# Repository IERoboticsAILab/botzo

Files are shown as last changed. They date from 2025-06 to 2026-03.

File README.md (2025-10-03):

<div align="center">
<h1>BOTZO 🐾</h1>

**`The good boy quadruped robot :)`**

<p align="center">
    <a href="https://www.instagram.com/botzo.ie/" target="_blank" rel="noopener noreferrer">
        
    </a>
    <a href="https://www.youtube.com/@Botzoie" target="_blank" rel="noopener noreferrer">
        
    </a>
    <a href="mailto:botzoteam@gmail.com">
        
    </a>
    <a href="">
        
    </a>

</p>

🚨🚧 **Project Under Construction!** 🚧🚨

Here's a sneak peek of our current progress:

</div>

> [!NOTE]
> A new documentation is currently being written 😃. It is already available [here](https://IERoboticsAILab.github.io/botzo/)

<p align="center">
    <a href="https://github.com/IERoboticsAILab/botzo/blob/main/docs/assets/botzo_new_final_design.png">
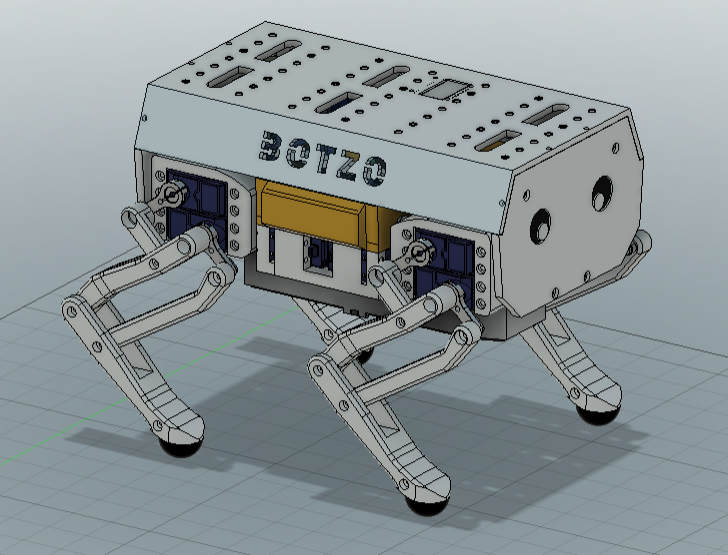
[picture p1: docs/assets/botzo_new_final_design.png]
Botzo
        
    </a>
</p>

> Stay tuned for updates and feel free to reach out with suggestions! Let's build Botzo together! 🛠️

## 🌟 **Welcome to the Botzo Project!**

**Botzo** is an autonomous quadruped robot designed to Navigate and Interact with its environment 🌍

This project combines sleek design, cutting-edge technology, and practical functionality to redefine robotic mobility.

## 📚 **Project Overview**

Botzo's development is divided into multiple phases, each focusing on specific aspects of its design, hardware, and software. We're actively working through these stages to bring the robot to life!

We stand in the middle of a trade of between high quality software and hardware, with low cost and affordability.

**Botzo is aimed to be a strong platform for everyone to replicate under 500€**

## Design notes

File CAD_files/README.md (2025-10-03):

<div align="center">
<h1>BOTZO 🐾</h1>

**`The good boy quadruped robot :)`**

<p align="center">
    <a href="https://www.instagram.com/botzo.ie/" target="_blank" rel="noopener noreferrer">
        
    </a>
    <a href="" target="_blank" rel="noopener noreferrer">
        
    </a>
    <a href="mailto:botzoteam@gmail.com">
        
    </a>
    <a href="">
        
    </a>

more about botzo [here](https://github.com/IERoboticsAILab/botzo)

for specific CAD documentation [here](https://ieroboticsailab.github.io/botzo/build/cad/cad-model/)

botzo

</p>
</div>

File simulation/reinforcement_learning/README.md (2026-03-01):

<div align="center">
<h1>BOTZO 🐾</h1>

**`The good boy quadruped robot :)`**

<p align="center">
    <a href="https://www.instagram.com/botzo.ie/" target="_blank" rel="noopener noreferrer">
        
    </a>
    <a href="" target="_blank" rel="noopener noreferrer">
        
    </a>
    <a href="mailto:botzoteam@gmail.com">
        
    </a>
    <a href="">
        
    </a>

</p>

</div>

more [here](https://github.com/IERoboticsAILab/botzo)

# Reinforcement Learning
In this repo we will explore how we teach botzo to walk

## Resources

- Genesis [link](https://genesis-world.readthedocs.io/en/latest/user_guide/index.html)
- Basics [link](https://youtu.be/f6LkEQsXGF8?si=eqC7IzNiBTZROUgm)
- theconstrucsim course Intermediate Generative AI for Robotics [link](https://app.theconstruct.ai/courses/intermediate-generative-ai-for-robotics-276/)
- theconstrucsim course Mastering Reinforcement Learning for Robotics [link](https://app.theconstruct.ai/courses/mastering-reinforcement-learning-for-robotics-286/)
- [Isaac Sim](https://docs.isaacsim.omniverse.nvidia.com/4.5.0/index.html)

# Isaac Sim

<p align="center">
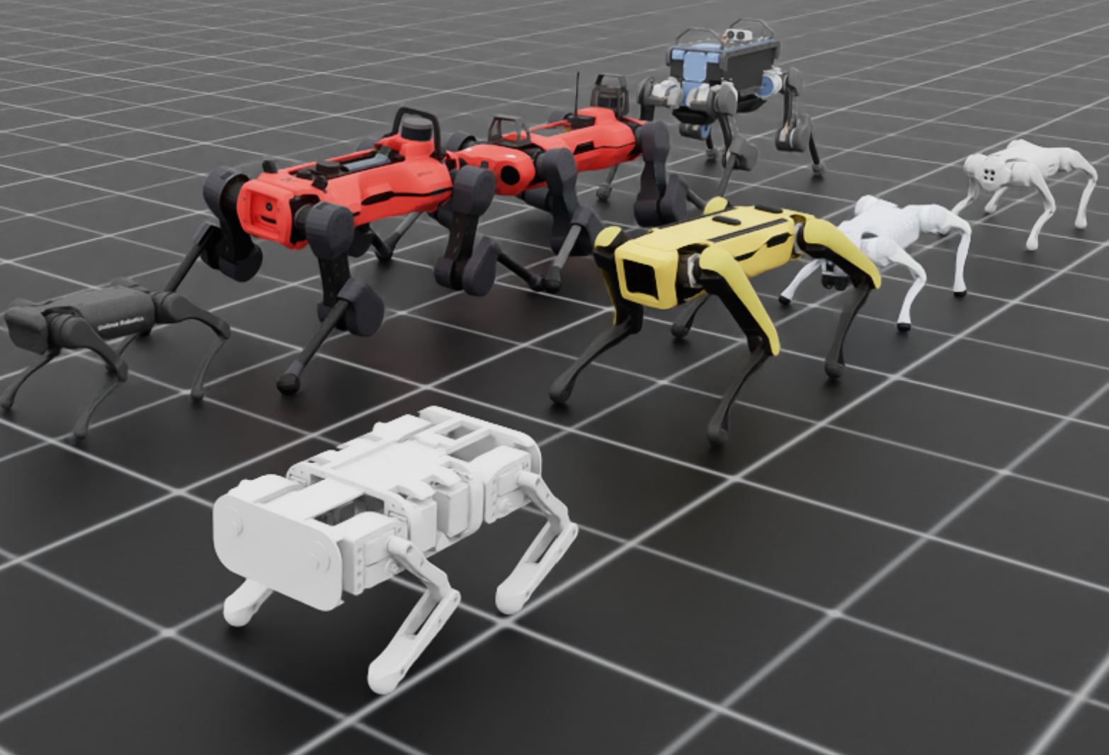
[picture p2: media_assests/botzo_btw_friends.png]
  
</p>
<p align="center"><em>Botzo between the giants & friends</em></p>

Computer specifications:
| Component | Specification |
|---|---|
| RAM | 64GB |
| GPU | RTX 4090 |
| VRAM | 16GB |
| OS | Windows 11 |
| Storage | 1TB |

>_Check system requirements compatibility and satisfaction with [this](https://download.isaacsim.omniverse.nvidia.com/isaac-sim-comp-check%404.5.0-rc.6%2Brelease.675.f1cca148.gl.windows-x86_64.release.zip)_

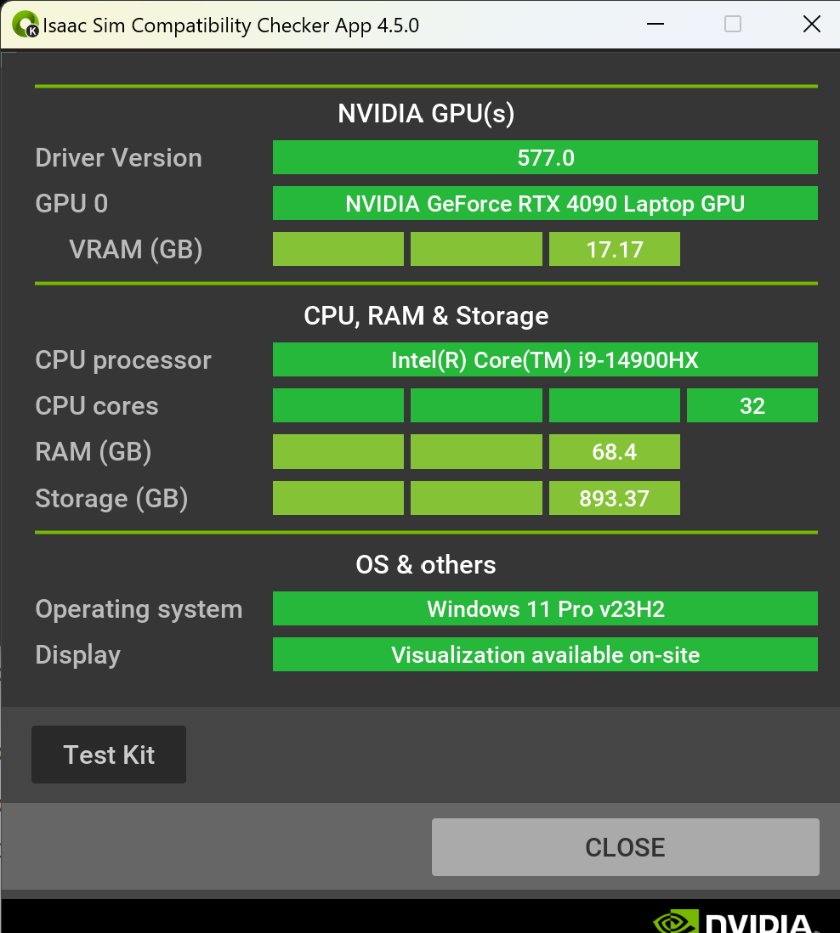
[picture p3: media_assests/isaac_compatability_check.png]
ours


Download [IsaacSim](https://download.isaacsim.omniverse.nvidia.com/isaac-sim-standalone%404.5.0-rc.36%2Brelease.19112.f59b3005.gl.windows-x86_64.release.zip) for your OS

```shell
mkdir C:\isaacsim
cd %USERPROFILE%/Downloads
tar -xvzf "isaac-sim-standalone@4.5.0-rc.36+release.19112.f59b3005.gl.windows-x86_64.release.zip" -C C:\isaacsim
cd C:\isaacsim
post_install.bat
isaac-sim.selector.bat
```
> [!NOTE] 
>The Isaac Sim app can be run directly via command line with `isaac-sim.bat`. Start new empty simulation.

> [!NOTE] 
>_extension_examples_ and _standalone_examples_ folder for the tutorials (ex: `.\python.bat .\standalone_examples\api\isaacsim.asset.importer.urdf\urdf_import.py`)

### Getting started with Isaac Sim

For more tutorials: Documentation [here](https://docs.isaacsim.omniverse.nvidia.com/4.5.0/introduction/quickstart_index.html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)

`conda activate env_isaaclab`

#### Import URDF

`.\python.bat ..\Users\grego\Desktop\GRINGO\botzo\botzo\simulation\reinforcment_learning\standalone_examples\import_botzo_urdf.py`

And then save it as a USD file. This file is used to import and manipulate your robot in Isaac Lab using python APIs. 

#### Import USD

`.\python.bat ..\Users\grego\Desktop\GRINGO\botzo\botzo\simulation\reinforcment_learning\standalone_examples\load_botzo_usd.py --usd_path "C:\Users\grego\Desktop\GRINGO\botzo\botzo\simulation\reinforcment_learning\botzo_USD\botzo_USD.usd"`

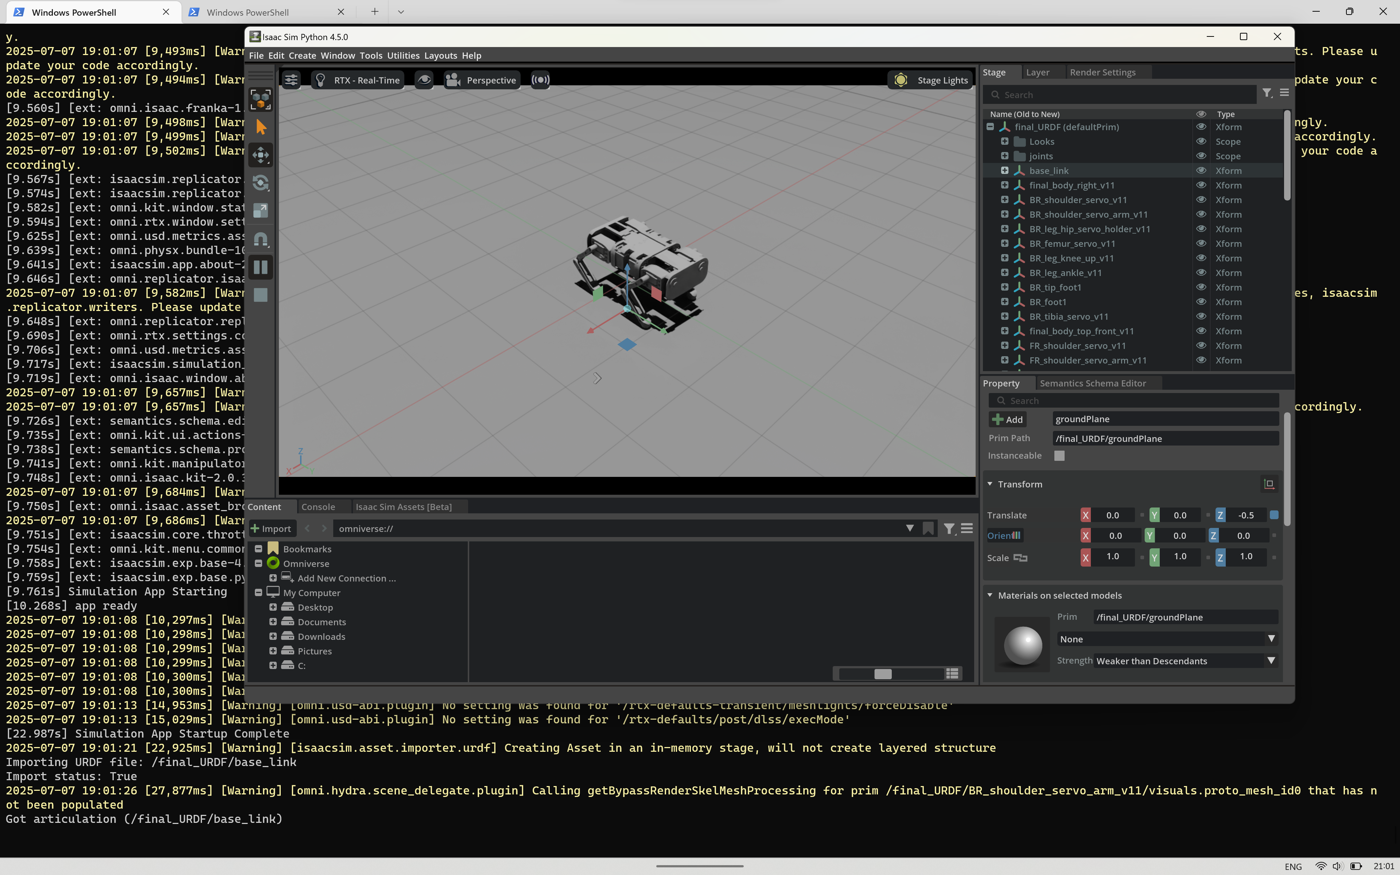
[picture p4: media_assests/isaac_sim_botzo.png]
result


<br>

<br>

# Isaac Lab

Isaac Lab is a collection of tools and libraries for building and simulating robots in Isaac Sim. It provides a set of APIs for creating robots, sensors, and environments, as well as tools for training and deploying reinforcement learning agents.

After the installation of Isaac Sim and Isaac Lab, you run examples such as:

```shell
(env_isaaclab) C:\Users\grego\Desktop\GRINGO\IsaacLab\IsaacLab>python scripts\tutorials\03_envs\create_quadruped_base_env.py
```

example

## Create your robot Configuration

To import your custom robot it is recomended to create a new Robot configuration python script.

Go to isaaclab/source/isaaclab_assets/robots and create a new python file with the name of your robot, for example `botzo.py`. Here we will import the USD file, and set robot properties.

<details>
<summary><b> `botzo.py` Code Robot configuration script </b></summary>

[Full Code](https://github.com/GRINGOLOCO7/IsaacLab/blob/main/source/isaaclab_assets/isaaclab_assets/robots/botzo.py)

```python

import isaaclab.sim as sim_utils
from isaaclab.actuators import ImplicitActuatorCfg
from isaaclab.assets.articulation import ArticulationCfg

stiffness = 2000.0     # N⋅m/rad - Very stiff for standing
damping = 200.0        # N⋅m⋅s/rad - High damping for stability
effort_limit_sim = 4.0 # N⋅m - Allow higher than rated for simulation
velocity_limit_sim = 10.0 # rad/s - Slightly higher for responsiveness

stiffness *= 40
damping *= 15
effort_limit_sim *= 25
velocity_limit_sim *= 10

BOTZO_CONFIG = ArticulationCfg(
    spawn=sim_utils.UsdFileCfg(
        usd_path="C:\\Users\\grego\\Desktop\\GRINGO\\botzo\\botzo\\simulation\\reinforcement_learning\\botzo_USD\\botzo_USD.usd",
        scale=(0.3, 0.3, 0.3),
    ),
    init_state=ArticulationCfg.InitialStateCfg(
        joint_pos={
            "BL_shoulder_joint": 0.0,
            "BL_femur_joint": 0.0,
            "BL_knee_joint": 0.0,

            "BR_shoulder_joint": 0.0,
            "BR_femur_joint": 0.0,
            "Revolute_43": 0.0,

            "FL_shoulder_joint": 0.0,
            "FL_femur_joint": 0.0,
            "FL_knee_joint": 0.0,

            "FR_shoulder_joint": 0.0,
            "FR_femur_joint": 0.0,
            "FR_knee_joint": 0.0,
        },
        pos=(0.0, 0.0, 0.25),
        # rotate 90 degrees around the x-axis
        rot=(-0.7071, 0.0, 0.0, 0.7071),  # Quaternion for 90 degrees rotation around x-axis
        # rotate upside down
        #rot=(0.0, 1.0, 0.0, 0.0),
    ),
    actuators={
        "BL_shoulder_act": ImplicitActuatorCfg(joint_names_expr=["BL_shoulder_joint"],effort_limit_sim=effort_limit_sim, velocity_limit_sim=velocity_limit_sim, stiffness=stiffness, damping=damping),
        "BL_femur_act": ImplicitActuatorCfg(joint_names_expr=["BL_femur_joint"], effort_limit_sim=effort_limit_sim, velocity_limit_sim=velocity_limit_sim, stiffness=stiffness, damping=damping),
        "BL_knee_act": ImplicitActuatorCfg(joint_names_expr=["BL_knee_joint"], effort_limit_sim=effort_limit_sim, velocity_limit_sim=velocity_limit_sim, stiffness=stiffness, damping=damping),
        "BR_shoulder_act": ImplicitActuatorCfg(joint_names_expr=["BR_shoulder_joint"], effort_limit_sim=effort_limit_sim, velocity_limit_sim=velocity_limit_sim, stiffness=stiffness, damping=damping),
        "BR_femur_act": ImplicitActuatorCfg(joint_names_expr=["BR_femur_joint"], effort_limit_sim=effort_limit_sim, velocity_limit_sim=velocity_limit_sim, stiffness=stiffness, damping=damping),
        "Revolute_43_act": ImplicitActuatorCfg(joint_names_expr=["Revolute_43"], effort_limit_sim=effort_limit_sim, velocity_limit_sim=velocity_limit_sim, stiffness=stiffness, damping=damping),
        "FL_shoulder_act": ImplicitActuatorCfg(joint_names_expr=["FL_shoulder_joint"], effort_limit_sim=effort_limit_sim, velocity_limit_sim=velocity_limit_sim, stiffness=stiffness, damping=damping),
        "FL_femur_act": ImplicitActuatorCfg(joint_names_expr=["FL_femur_joint"], effort_limit_sim=effort_limit_sim, velocity_limit_sim=velocity_limit_sim, stiffness=stiffness, damping=damping),
        "FL_knee_act": ImplicitActuatorCfg(joint_names_expr=["FL_knee_joint"], effort_limit_sim=effort_limit_sim, velocity_limit_sim=velocity_limit_sim, stiffness=stiffness, damping=damping),
        "FR_shoulder_act": ImplicitActuatorCfg(joint_names_expr=["FR_shoulder_joint"], effort_limit_sim=effort_limit_sim, velocity_limit_sim=velocity_limit_sim, stiffness=stiffness, damping=damping),
        "FR_femur_act": ImplicitActuatorCfg(joint_names_expr=["FR_femur_joint"], effort_limit_sim=effort_limit_sim, velocity_limit_sim=velocity_limit_sim, stiffness=stiffness, damping=damping),
        "FR_knee_act": ImplicitActuatorCfg(joint_names_expr=["FR_knee_joint"], effort_limit_sim=effort_limit_sim, velocity_limit_sim=velocity_limit_sim, stiffness=stiffness, damping=damping),
    },
)

```

</details>

<br>

<details>
<summary><b> `dofrobot.py` Code Robot configuration script </b></summary>

[Full Code](https://github.com/GRINGOLOCO7/IsaacLab/blob/main/source/isaaclab_assets/isaaclab_assets/robots/dofrobot.py)

```python

import isaaclab.sim as sim_utils
from isaaclab.actuators import ImplicitActuatorCfg
from isaaclab.assets.articulation import ArticulationCfg
from isaaclab.utils.assets import ISAAC_NUCLEUS_DIR

DOFBOT_CONFIG = ArticulationCfg(
    spawn=sim_utils.UsdFileCfg(
        usd_path=f"{ISAAC_NUCLEUS_DIR}/Robots/Dofbot/dofbot.usd",
        rigid_props=sim_utils.RigidBodyPropertiesCfg(
            disable_gravity=False,
            max_depenetration_velocity=5.0,
        ),
        articulation_props=sim_utils.ArticulationRootPropertiesCfg(
            enabled_self_collisions=True, solver_position_iteration_count=8, solver_velocity_iteration_count=0
        ),
    ),
    init_state=ArticulationCfg.InitialStateCfg(
        joint_pos={
            "joint1": 0.0,
            "joint2": 0.0,
            "joint3": 0.0,
            "joint4": 0.0,
        },
        pos=(0.25, -0.25, 0.0),
    ),
    actuators={
        "front_joints": ImplicitActuatorCfg(
            joint_names_expr=["joint[1-2]"],
            effort_limit_sim=100.0,
            velocity_limit_sim=100.0,
            stiffness=10000.0,
            damping=100.0,
        ),
        "joint3_act": ImplicitActuatorCfg(
            joint_names_expr=["joint3"],
            effort_limit_sim=100.0,
            velocity_limit_sim=100.0,
            stiffness=10000.0,
            damping=100.0,
        ),
        "joint4_act": ImplicitActuatorCfg(
            joint_names_expr=["joint4"],
            effort_limit_sim=100.0,
            velocity_limit_sim=100.0,
            stiffness=10000.0,
            damping=100.0,
        ),
    },
)

```

</details>

<br>

<details>
<summary><b> `jetbot.py` Code Robot configuration script </b></summary>

[Full Code](https://github.com/GRINGOLOCO7/IsaacLab/blob/main/source/isaaclab_assets/isaaclab_assets/robots/jetbot.py)

```python

import isaaclab.sim as sim_utils
from isaaclab.assets import ArticulationCfg
from isaaclab.actuators import ImplicitActuatorCfg
from isaaclab.utils.assets import ISAAC_NUCLEUS_DIR

JETBOT_CONFIG = ArticulationCfg(
    spawn=sim_utils.UsdFileCfg(usd_path=f"{ISAAC_NUCLEUS_DIR}/Robots/Jetbot/jetbot.usd"),
    actuators={"wheel_acts": ImplicitActuatorCfg(joint_names_expr=[".*"], damping=None, stiffness=None)},
)

```

</details>

### Use your robot configuration

Now that we configured our robot, we can simply import it and use it in any python file we want

1. Import robot config: `from isaaclab_assets.robots.botzo import BOTZO_CONFIG`
2. Spawn robot: `Botzo = BOTZO_CONFIG.replace(prim_path="{ENV_REGEX_NS}/Botzo")`
3. Now you can move and interact with it

#### Our Examples:

1. `python scripts\demos\quadrupeds.py`

<details>
<summary><b> Spawn various robots </b></summary>

[Full Code](https://github.com/GRINGOLOCO7/IsaacLab/blob/main/scripts/demos/quadrupeds.py)

```python
# Copyright (c) 2022-2025, The Isaac Lab Project Developers (https://github.com/isaac-sim/IsaacLab/blob/main/CONTRIBUTORS.md).
# All rights reserved.
#
# SPDX-License-Identifier: BSD-3-Clause

"""
This script demonstrates different legged robots.

.. code-block:: bash

    # Usage
    ./isaaclab.sh -p scripts/demos/quadrupeds.py

"""

"""Launch Isaac Sim Simulator first."""

import argparse

from isaaclab.app import AppLauncher

# add argparse arguments
parser = argparse.ArgumentParser(description="This script demonstrates different legged robots.")
# append AppLauncher cli args
AppLauncher.add_app_launcher_args(parser)
# parse the arguments
args_cli = parser.parse_args()

# launch omniverse app
app_launcher = AppLauncher(args_cli)
simulation_app = app_launcher.app

"""Rest everything follows."""

import numpy as np
import torch

import isaacsim.core.utils.prims as prim_utils

import isaaclab.sim as sim_utils
from isaaclab.assets import Articulation

##
# Pre-defined configs
##
from isaaclab_assets.robots.anymal import ANYMAL_B_CFG, ANYMAL_C_CFG, ANYMAL_D_CFG  # isort:skip
from isaaclab_assets.robots.spot import SPOT_CFG  # isort:skip
from isaaclab_assets.robots.unitree import UNITREE_A1_CFG, UNITREE_GO1_CFG, UNITREE_GO2_CFG  # isort:skip
from isaaclab_assets.robots.botzo import BOTZO_CONFIG  # isort:skip

def define_origins(num_origins: int, spacing: float) -> list[list[float]]:
    """Defines the origins of the scene."""
    # create tensor based on number of environments
    env_origins = torch.zeros(num_origins, 3)
    # create a grid of origins
    num_cols = np.floor(np.sqrt(num_origins))
    num_rows = np.ceil(num_origins / num_cols)
    xx, yy = torch.meshgrid(torch.arange(num_rows), torch.arange(num_cols), indexing="xy")
    env_origins[:, 0] = spacing * xx.flatten()[:num_origins] - spacing * (num_rows - 1) / 2
    env_origins[:, 1] = spacing * yy.flatten()[:num_origins] - spacing * (num_cols - 1) / 2
    env_origins[:, 2] = 0.0
    # return the origins
    return env_origins.tolist()

def design_scene() -> tuple[dict, list[list[float]]]:
    """Designs the scene."""
    # Ground-plane
    cfg = sim_utils.GroundPlaneCfg()
    cfg.func("/World/defaultGroundPlane", cfg)
    # Lights
    cfg = sim_utils.DomeLightCfg(intensity=2000.0, color=(0.75, 0.75, 0.75))
    cfg.func("/World/Light", cfg)

    # Create separate groups called "Origin1", "Origin2", "Origin3"
    # Each group will have a mount and a robot on top of it
    origins = define_origins(num_origins=8, spacing=1.25)

    # Origin 1 with Anymal B
    prim_utils.create_prim("/World/Origin1", "Xform", translation=origins[0])
    # -- Robot
    anymal_b = Articulation(ANYMAL_B_CFG.replace(prim_path="/World/Origin1/Robot"))

    # Origin 2 with Anymal C
    prim_utils.create_prim("/World/Origin2", "Xform", translation=origins[1])
    # -- Robot
    anymal_c = Articulation(ANYMAL_C_CFG.replace(prim_path="/World/Origin2/Robot"))

    # Origin 3 with Anymal D
    prim_utils.create_prim("/World/Origin3", "Xform", translation=origins[2])
    # -- Robot
    anymal_d = Articulation(ANYMAL_D_CFG.replace(prim_path="/World/Origin3/Robot"))

    # Origin 4 with Unitree A1
    prim_utils.create_prim("/World/Origin4", "Xform", translation=origins[3])
    # -- Robot
    unitree_a1 = Articulation(UNITREE_A1_CFG.replace(prim_path="/World/Origin4/Robot"))

    # Origin 5 with Unitree Go1
    prim_utils.create_prim("/World/Origin5", "Xform", translation=origins[4])
    # -- Robot
    unitree_go1 = Articulation(UNITREE_GO1_CFG.replace(prim_path="/World/Origin5/Robot"))

    # Origin 6 with Unitree Go2
    prim_utils.create_prim("/World/Origin6", "Xform", translation=origins[5])
    # -- Robot
    unitree_go2 = Articulation(UNITREE_GO2_CFG.replace(prim_path="/World/Origin6/Robot"))

    # Origin 7 with Boston Dynamics Spot
    prim_utils.create_prim("/World/Origin7", "Xform", translation=origins[6])
    # -- Robot
    spot = Articulation(SPOT_CFG.replace(prim_path="/World/Origin7/Robot"))

    # Origin 8 with Botzo
    prim_utils.create_prim("/World/Origin8", "Xform", translation=origins[7])
    # -- Robot
    botzo = Articulation(BOTZO_CONFIG.replace(prim_path="/World/Origin8/Robot"))

    # return the scene information
    scene_entities = {
        "anymal_b": anymal_b,
        "anymal_c": anymal_c,
        "anymal_d": anymal_d,
        "unitree_a1": unitree_a1,
        "unitree_go1": unitree_go1,
        "unitree_go2": unitree_go2,
        "spot": spot,
        "botzo": botzo,
    }
    return scene_entities, origins

def run_simulator(sim: sim_utils.SimulationContext, entities: dict[str, Articulation], origins: torch.Tensor):
    """Runs the simulation loop."""
    # Define simulation stepping
    sim_dt = sim.get_physics_dt()
    sim_time = 0.0
    count = 0
    # Simulate physics
    while simulation_app.is_running():
        # reset
        if count % 200 == 0:
            # reset counters
            sim_time = 0.0
            count = 0
            # reset robots
            for index, robot in enumerate(entities.values()):
                # root state
                root_state = robot.data.default_root_state.clone()
                root_state[:, :3] += origins[index]
                robot.write_root_pose_to_sim(root_state[:, :7])
                robot.write_root_velocity_to_sim(root_state[:, 7:])
                # joint state
                joint_pos, joint_vel = robot.data.default_joint_pos.clone(), robot.data.default_joint_vel.clone()
                robot.write_joint_state_to_sim(joint_pos, joint_vel)
                # reset the internal state
                robot.reset()
            print("[INFO]: Resetting robots state...")
        # apply default actions to the quadrupedal robots
        for robot in entities.values():
            # generate random joint positions
            joint_pos_target = robot.data.default_joint_pos + torch.randn_like(robot.data.joint_pos) * 0.1
            # apply action to the robot
            robot.set_joint_position_target(joint_pos_target)
            # write data to sim
            robot.write_data_to_sim()
        # perform step
        sim.step()
        # update sim-time
        sim_time += sim_dt
        count += 1
        # update buffers
        for robot in entities.values():
            robot.update(sim_dt)

def main():
    """Main function."""

    # Initialize the simulation context
    sim = sim_utils.SimulationContext(sim_utils.SimulationCfg(dt=0.01))
    # Set main camera
    sim.set_camera_view(eye=[2.5, 2.5, 2.5], target=[0.0, 0.0, 0.0])
    # design scene
    scene_entities, scene_origins = design_scene()
    scene_origins = torch.tensor(scene_origins, device=sim.device)
    # Play the simulator
    sim.reset()
    # Now we are ready!
    print("[INFO]: Setup complete...")
    # Run the simulator
    run_simulator(sim, scene_entities, scene_origins)

if __name__ == "__main__":
    # run the main function
    main()
    # close sim app
    simulation_app.close()

```

</details>

2. `python scripts\tutorials\01_assets\add_new_robot.py`

<details>
<summary><b> Spawn various robots and move them </b></summary>

[full Code](https://github.com/GRINGOLOCO7/IsaacLab/blob/main/scripts/tutorials/01_assets/add_new_robot.py)

```python
# Copyright (c) 2022-2025, The Isaac Lab Project Developers (https://github.com/isaac-sim/IsaacLab/blob/main/CONTRIBUTORS.md).
# All rights reserved.
#
# SPDX-License-Identifier: BSD-3-Clause

import argparse

from isaaclab.app import AppLauncher

# add argparse arguments
parser = argparse.ArgumentParser(
    description="This script demonstrates adding a custom robot to an Isaac Lab environment."
)
parser.add_argument("--num_envs", type=int, default=1, help="Number of environments to spawn.")
# append AppLauncher cli args
AppLauncher.add_app_launcher_args(parser)
# parse the arguments
args_cli = parser.parse_args()

# launch omniverse app
app_launcher = AppLauncher(args_cli)
simulation_app = app_launcher.app

import numpy as np
import torch

import isaaclab.sim as sim_utils
from isaaclab.actuators import ImplicitActuatorCfg
from isaaclab.assets import AssetBaseCfg
from isaaclab.assets.articulation import ArticulationCfg
from isaaclab.scene import InteractiveScene, InteractiveSceneCfg
from isaaclab.utils.assets import ISAAC_NUCLEUS_DIR

from isaaclab_assets.robots.botzo import BOTZO_CONFIG # source\isaaclab_assets\isaaclab_assets\robots\botzo.py

JETBOT_CONFIG = ArticulationCfg(
    spawn=sim_utils.UsdFileCfg(usd_path=f"{ISAAC_NUCLEUS_DIR}/Robots/Jetbot/jetbot.usd"),
    actuators={"wheel_acts": ImplicitActuatorCfg(joint_names_expr=[".*"], damping=None, stiffness=None)},
)

DOFBOT_CONFIG = ArticulationCfg(
    spawn=sim_utils.UsdFileCfg(
        usd_path=f"{ISAAC_NUCLEUS_DIR}/Robots/Dofbot/dofbot.usd",
        rigid_props=sim_utils.RigidBodyPropertiesCfg(
            disable_gravity=False,
            max_depenetration_velocity=5.0,
        ),
        articulation_props=sim_utils.ArticulationRootPropertiesCfg(
            enabled_self_collisions=True, solver_position_iteration_count=8, solver_velocity_iteration_count=0
        ),
    ),
    init_state=ArticulationCfg.InitialStateCfg(
        joint_pos={
            "joint1": 0.0,
            "joint2": 0.0,
            "joint3": 0.0,
            "joint4": 0.0,
        },
        pos=(0.25, -0.25, 0.0),
    ),
    actuators={
        "front_joints": ImplicitActuatorCfg(
            joint_names_expr=["joint[1-2]"],
            effort_limit_sim=100.0,
            velocity_limit_sim=100.0,
            stiffness=10000.0,
            damping=100.0,
        ),
        "joint3_act": ImplicitActuatorCfg(
            joint_names_expr=["joint3"],
            effort_limit_sim=100.0,
            velocity_limit_sim=100.0,
            stiffness=10000.0,
            damping=100.0,
        ),
        "joint4_act": ImplicitActuatorCfg(
            joint_names_expr=["joint4"],
            effort_limit_sim=100.0,
            velocity_limit_sim=100.0,
            stiffness=10000.0,
            damping=100.0,
        ),
    },
)

class NewRobotsSceneCfg(InteractiveSceneCfg):
    """Designs the scene."""

    # Ground-plane
    ground = AssetBaseCfg(prim_path="/World/defaultGroundPlane", spawn=sim_utils.GroundPlaneCfg())

    # lights
    dome_light = AssetBaseCfg(
        prim_path="/World/Light", spawn=sim_utils.DomeLightCfg(intensity=3000.0, color=(0.75, 0.75, 0.75))
    )

    # robot
    Jetbot = JETBOT_CONFIG.replace(prim_path="{ENV_REGEX_NS}/Jetbot")
    Dofbot = DOFBOT_CONFIG.replace(prim_path="{ENV_REGEX_NS}/Dofbot")
    Botzo = BOTZO_CONFIG.replace(prim_path="{ENV_REGEX_NS}/Botzo")

def run_simulator(sim: sim_utils.SimulationContext, scene: InteractiveScene):
    sim_dt = sim.get_physics_dt()
    sim_time = 0.0
    count = 0

    while simulation_app.is_running():
        # reset
        if count % 500 == 0:
            # reset counters
            count = 0
            # reset the scene entities to their initial positions offset by the environment origins
            root_jetbot_state = scene["Jetbot"].data.default_root_state.clone()
            root_jetbot_state[:, :3] += scene.env_origins
            root_dofbot_state = scene["Dofbot"].data.default_root_state.clone()
            root_dofbot_state[:, :3] += scene.env_origins
            robot_botzo_state = scene["Botzo"].data.default_root_state.clone()
            robot_botzo_state[:, :3] += scene.env_origins

            # copy the default root state to the sim for the jetbot's orientation and velocity
            scene["Jetbot"].write_root_pose_to_sim(root_jetbot_state[:, :7])
            scene["Jetbot"].write_root_velocity_to_sim(root_jetbot_state[:, 7:])
            scene["Dofbot"].write_root_pose_to_sim(root_dofbot_state[:, :7])
            scene["Dofbot"].write_root_velocity_to_sim(root_dofbot_state[:, 7:])
            scene["Botzo"].write_root_pose_to_sim(robot_botzo_state[:, :7])
            scene["Botzo"].write_root_velocity_to_sim(robot_botzo_state[:, 7:])

            # copy the default joint states to the sim
            joint_pos, joint_vel = (
                scene["Jetbot"].data.default_joint_pos.clone(),
                scene["Jetbot"].data.default_joint_vel.clone(),
            )
            scene["Jetbot"].write_joint_state_to_sim(joint_pos, joint_vel)
            joint_pos, joint_vel = (
                scene["Dofbot"].data.default_joint_pos.clone(),
                scene["Dofbot"].data.default_joint_vel.clone(),
            )
            scene["Dofbot"].write_joint_state_to_sim(joint_pos, joint_vel)
            joint_pos, joint_vel = (
                scene["Botzo"].data.default_joint_pos.clone(),
                scene["Botzo"].data.default_joint_vel.clone(),
            )
            scene["Botzo"].write_joint_state_to_sim(joint_pos, joint_vel)
            # clear internal buffers
            scene.reset()
            print("[INFO]: Resetting Jetbot and Dofbot state...")

        # drive around
        if count % 100 < 75:
            # Drive straight by setting equal wheel velocities
            action = torch.Tensor([[10.0, 10.0]])
        else:
            # Turn by applying different velocities
            action = torch.Tensor([[5.0, -5.0]])

        scene["Jetbot"].set_joint_velocity_target(action)

        # wave
        wave_action = scene["Dofbot"].data.default_joint_pos
        wave_action[:, 0:4] = 0.25 * np.sin(2 * np.pi * 0.5 * sim_time)
        scene["Dofbot"].set_joint_position_target(wave_action)
        # move botzo
        botzo_action = scene["Botzo"].data.default_joint_pos
        botzo_action[:, 0:3] = 0.25 * np.sin(2 * np.pi * 0.5 * sim_time)
        botzo_action[:, 3:6] = 0.25 * np.cos(2 * np.pi * 0.5 * sim_time)
        scene["Botzo"].set_joint_position_target(botzo_action)

        scene.write_data_to_sim()
        sim.step()
        sim_time += sim_dt
        count += 1
        scene.update(sim_dt)

def main():
    """Main function."""
    # Initialize the simulation context
    sim_cfg = sim_utils.SimulationCfg(device=args_cli.device)
    sim = sim_utils.SimulationContext(sim_cfg)

    sim.set_camera_view([3.5, 0.0, 3.2], [0.0, 0.0, 0.5])
    # design scene
    scene_cfg = NewRobotsSceneCfg(args_cli.num_envs, env_spacing=2.0)
    scene = InteractiveScene(scene_cfg)
    # Play the simulator
    sim.reset()
    # Now we are ready!
    print("[INFO]: Setup complete...")
    # Run the simulator
    run_simulator(sim, scene)

if __name__ == "__main__":
    main()
    simulation_app.close()

```

</details>

3. `python scripts\tutorials\01_assets\botzo_move_IK.py `

<details>
<summary><b> Create digital twin of botzo and move it with our IK </b></summary>

https://github.com/GRINGOLOCO7/IsaacLab/blob/main/scripts/tutorials/01_assets/botzo_move_IK.py

```python
import argparse

from isaaclab.app import AppLauncher

# add argparse arguments
parser = argparse.ArgumentParser(
    description="This script demonstrates adding a custom robot to an Isaac Lab environment."
)
parser.add_argument("--num_envs", type=int, default=1, help="Number of environments to spawn.")
# append AppLauncher cli args
AppLauncher.add_app_launcher_args(parser)
# parse the arguments
args_cli = parser.parse_args()

# launch omniverse app
app_launcher = AppLauncher(args_cli)
simulation_app = app_launcher.app

import numpy as np
import torch

import isaaclab.sim as sim_utils
from isaaclab.actuators import ImplicitActuatorCfg
from isaaclab.assets import AssetBaseCfg
from isaaclab.assets.articulation import ArticulationCfg
from isaaclab.scene import InteractiveScene, InteractiveSceneCfg
from isaaclab.utils.assets import ISAAC_NUCLEUS_DIR

from isaaclab_assets.robots.botzo import BOTZO_CONFIG # source\isaaclab_assets\isaaclab_assets\robots\botzo.py
from botzo_IK_solver import *
import math

class NewRobotsSceneCfg(InteractiveSceneCfg):
    """Designs the scene."""

    # Ground-plane
    ground = AssetBaseCfg(prim_path="/World/defaultGroundPlane", spawn=sim_utils.GroundPlaneCfg())

    # lights
    dome_light = AssetBaseCfg(
        prim_path="/World/Light", spawn=sim_utils.DomeLightCfg(intensity=3000.0, color=(0.75, 0.75, 0.75))
    )

    # robot
    Botzo = BOTZO_CONFIG.replace(prim_path="{ENV_REGEX_NS}/Botzo")

def run_simulator(sim: sim_utils.SimulationContext, scene: InteractiveScene):
    sim_dt = sim.get_physics_dt()
    sim_time = 0.0
    count = 0

    idx = 0

    while simulation_app.is_running():
        # reset
        if count % 500 == 0:
            # reset counters
            count = 0
            # reset the scene entities to their initial positions offset by the environment origins
            robot_botzo_state = scene["Botzo"].data.default_root_state.clone()
            robot_botzo_state[:, :3] += scene.env_origins

            # copy the default root state to the sim for the jetbot's orientation and velocity
            scene["Botzo"].write_root_pose_to_sim(robot_botzo_state[:, :7])
            scene["Botzo"].write_root_velocity_to_sim(robot_botzo_state[:, 7:])

            # copy the default joint states to the sim
            joint_pos, joint_vel = (
                scene["Botzo"].data.default_joint_pos.clone(),
                scene["Botzo"].data.default_joint_vel.clone(),
            )
            scene["Botzo"].write_joint_state_to_sim(joint_pos, joint_vel)
            # clear internal buffers
            scene.reset()
            print("[INFO]: Resetting Botzo state...")

        # move botzo
        '''
        tensor([[
                0  -  BL_shoulder, 
                1  -  BR_shoulder, 
                2  -  FL_shoulder, 
                3  -  FR_shoulder, 

                4  -  BL_femur, 
                5  -  BR_femur, 
                6  -  FL_femur, 
                7  -  FR_femur, 

                8  -  BL_knee, 
                9  -  BR_knee, 
                10 -  FL_knee, 
                11 -  FR_knee
                ]], device='cuda:0')
        '''
        botzo_action = scene["Botzo"].data.default_joint_pos
        # print the difference btw current pos and target pos
        #print(f"{'='*10}\nCurrent: {scene['Botzo'].data.joint_pos},\nTarget: {botzo_action}\n{'='*10}\n\n\n")
        tolerance = math.radians(5.0)
        if not torch.all(torch.abs(scene["Botzo"].data.joint_pos - botzo_action) < tolerance):
            #print("position not reached")
            pass
        else:
            #print("position reached, pass to new target")
            # calculate angles
            FR_s_f_t = legIK(forward_targets_FR_BL[idx][0], forward_targets_FR_BL[idx][1], forward_targets_FR_BL[idx][2])
            FR_angle_shoulder, FR_angle_femur, FR_angle_knee = FR_s_f_t
            target_FR_angle_shoulder = math.radians(real_sim_angle(FR_angle_shoulder,joint_ids["FR"]["shoulder"]))
            target_FR_angle_femur = math.radians(real_sim_angle(FR_angle_femur, joint_ids["FR"]["femur"]))
            target_FR_angle_knee = math.radians(real_sim_angle(FR_angle_knee, joint_ids["FR"]["knee"]))
            FL_s_f_t = legIK(forward_targets_FL_BR[idx][0], forward_targets_FL_BR[idx][1], forward_targets_FL_BR[idx][2])
            FL_angle_shoulder, FL_angle_femur, FL_angle_knee = FL_s_f_t
            target_FL_angle_shoulder = math.radians(real_sim_angle(FL_angle_shoulder,joint_ids["FL"]["shoulder"]))
            target_FL_angle_femur = math.radians(real_sim_angle(FL_angle_femur, joint_ids["FL"]["femur"]))
            target_FL_angle_knee = math.radians(real_sim_angle(FL_angle_knee, joint_ids["FL"]["knee"]))
            BR_s_f_t = legIK(forward_targets_FL_BR[idx][0], forward_targets_FL_BR[idx][1], forward_targets_FL_BR[idx][2])
            BR_angle_shoulder, BR_angle_femur, BR_angle_knee = BR_s_f_t
            target_BR_angle_shoulder = math.radians(real_sim_angle(BR_angle_shoulder,joint_ids["BR"]["shoulder"]))
            target_BR_angle_femur = math.radians(real_sim_angle(BR_angle_femur, joint_ids["BR"]["femur"]))
            target_BR_angle_knee = math.radians(real_sim_angle(BR_angle_knee, joint_ids["BR"]["knee"]))
            BL_s_f_t = legIK(forward_targets_FR_BL[idx][0], forward_targets_FR_BL[idx][1], forward_targets_FR_BL[idx][2])
            BL_angle_shoulder, BL_angle_femur, BL_angle_knee = BL_s_f_t
            target_BL_angle_shoulder = math.radians(real_sim_angle(BL_angle_shoulder,joint_ids["BL"]["shoulder"]))
            target_BL_angle_femur = math.radians(real_sim_angle(BL_angle_femur, joint_ids["BL"]["femur"]))
            target_BL_angle_knee = math.radians(real_sim_angle(BL_angle_knee, joint_ids["BL"]["knee"]))
            
            if idx >= len(forward_targets_FR_BL)-1:
                idx = 0  # Reset index if it exceeds the number of targets
            else:
                idx += 1
        # set the angles to the botzo action
        botzo_action[:, 0] = target_BL_angle_shoulder
        botzo_action[:, 1] = target_BR_angle_shoulder
        botzo_action[:, 2] = target_FL_angle_shoulder
        botzo_action[:, 3] = target_FR_angle_shoulder
        botzo_action[:, 4] = target_BL_angle_femur
        botzo_action[:, 5] = target_BR_angle_femur
        botzo_action[:, 6] = target_FL_angle_femur
        botzo_action[:, 7] = target_FR_angle_femur
        botzo_action[:, 8] = target_BL_angle_knee
        botzo_action[:, 9] = target_BR_angle_knee
        botzo_action[:, 10] = target_FL_angle_knee
        botzo_action[:, 11] = target_FR_angle_knee
        # write the action to the sim
        scene["Botzo"].set_joint_position_target(botzo_action)

        scene.write_data_to_sim()
        sim.step()
        sim_time += sim_dt
        count += 1
        scene.update(sim_dt)

def main():
    """Main function."""
    # Initialize the simulation context
    sim_cfg = sim_utils.SimulationCfg(device=args_cli.device)
    sim = sim_utils.SimulationContext(sim_cfg)

    sim.set_camera_view([3.5, 0.0, 3.2], [0.0, 0.0, 0.5])
    # design scene
    scene_cfg = NewRobotsSceneCfg(args_cli.num_envs, env_spacing=2.0)
    scene = InteractiveScene(scene_cfg)
    # Play the simulator
    sim.reset()
    # Now we are ready!
    print("[INFO]: Setup complete...")
    # Run the simulator
    run_simulator(sim, scene)

if __name__ == "__main__":
    main()
    simulation_app.close()

```

</details>

add a note here:

> [!NOTE]
> Remember to add `botzo_IK_solver.py` in the same directory (`scripts\tutorials\01_assets\`), so we can use the inverse kinematics solver for the Botzo robot. Code can be found [here](https://github.com/IERoboticsAILab/botzo/blob/main/simulation/src/IK_solver.py or [here](https://github.com/GRINGOLOCO7/IsaacLab/blob/main/scripts/tutorials/01_assets/botzo_IK_solver.py))

4. `python scripts\tutorials\05_controllers\botzo_diff_ik.py`

<details>
<summary><b> Create digital twin of botzo and move it with NVIDIA IK tools </b></summary>

[Full Code](https://github.com/GRINGOLOCO7/IsaacLab/blob/main/scripts/tutorials/05_controllers/botzo_diff_ik.py)

```python
work in progress
```

</details>

## Isaac Lab RL templates

By having the robot config file setup, now we can create a RL agent environment template, that will contain all the necessary scripts to run different RL algorithm to teach our robot how to perfom our desire task.

This termplates can be found in the `isaaclab/source/isaaclab_tasks` directory.

They are divided into direct and manager based (both with their pros and cons (check isaac lab documentation for more infos)).

Each template is designed to be easily customizable for different robot configurations and tasks. They contain agents, that refer to the RL algorithm that we will use to train our robot to perform our desire task. This algorithm are taken form Stable Baselines3 or Skrl.

Then we have the **environment configuration** files, which define the specific settings and parameters for each environment. These files are crucial for ensuring that the RL agent can effectively interact with the simulation and learn from it (**environment properties**).  And the **environment** files are also responsible for defining the observation and action spaces for the RL agent (**reset, get reward, observations, etc...**).

<details>
<summary><b>Jetbot RL example</b></summary>

[Full Code Jetbot Template](https://github.com/GRINGOLOCO7/IsaacLab/tree/main/source/isaaclab_tasks/isaaclab_tasks/direct/jetbot_controller)

Isaac Lab Documentation [here](https://isaac-sim.github.io/IsaacLab/main/source/setup/walkthrough/index.html)

### Train Jetbot to drive forward

example

```shell
isaaclab.bat --new
python scripts\environments\list_envs.py      # find for the task/project/template just created
# if you don't find it try this comand:  python -m pip install -e source\isaaclab_tasks
python scripts\reinforcement_learning\skrl\train.py --task=Isaac-Jetbot-Marl-Direct-v0
python scripts\reinforcement_learning\skrl\play.py --task=Isaac-Jetbot-Marl-Direct-v0
```

### Train Jetbot to follow commands (Controller with RL)

Objective: now start modifying our observations and rewards in order to train a policy to act as a controller for the Jetbot. As a user, we would like to be able to specify the desired direction for the Jetbot to drive, and have the wheels turn such that the robot drives in that specified direction as fast as possible.

1. Create template:

```shell
isaaclab.bat --new # will create new task such as: Generating 'Isaac-Jetbot-Controller-Direct-v0'
```

2. Check the task:

```shell
python scripts\environments\list_envs.py
```

3. create the logic for setting commands for each Jetbot on the stage. Each command will be a unit vector, and we need one for every clone of the robot on the stage, which means a tensor of shape [num_envs, 3]. And setup visualizations, so we can more easily tell what the policy is doing during training and inference. So we define two arrow VisualizationMarkers: one to represent the “forward” direction of the robot, and one to represent the command direction. When the policy is fully trained, these arrows should be aligned! 

4. Add arrow visualization to the `*_env.py`:

```python
from isaaclab.markers import VisualizationMarkers, VisualizationMarkersCfg
from isaaclab.utils.assets import ISAAC_NUCLEUS_DIR
import isaaclab.utils.math as math_utils

def define_markers() -> VisualizationMarkers:
    """Define markers with various different shapes."""
    marker_cfg = VisualizationMarkersCfg(
        prim_path="/Visuals/myMarkers",
        markers={
                "forward": sim_utils.UsdFileCfg(
                    usd_path=f"{ISAAC_NUCLEUS_DIR}/Props/UIElements/arrow_x.usd",
                    scale=(0.25, 0.25, 0.5),
                    visual_material=sim_utils.PreviewSurfaceCfg(diffuse_color=(0.0, 1.0, 1.0)),
                ),
                "command": sim_utils.UsdFileCfg(
                    usd_path=f"{ISAAC_NUCLEUS_DIR}/Props/UIElements/arrow_x.usd",
                    scale=(0.25, 0.25, 0.5),
                    visual_material=sim_utils.PreviewSurfaceCfg(diffuse_color=(1.0, 0.0, 0.0)),
                ),
        },
    )
    return VisualizationMarkers(cfg=marker_cfg)
```

5. expand the initialization and setup steps to construct the data we need for tracking the commands as well as the marker positions and rotations. Replace the contents of _setup_scene with the following

```python
def _setup_scene(self):
    self.robot = Articulation(self.cfg.robot_cfg)
    # add ground plane
    spawn_ground_plane(prim_path="/World/ground", cfg=GroundPlaneCfg())
    # clone and replicate
    self.scene.clone_environments(copy_from_source=False)
    # add articulation to scene
    self.scene.articulations["robot"] = self.robot
    # add lights
    light_cfg = sim_utils.DomeLightCfg(intensity=2000.0, color=(0.75, 0.75, 0.75))
    light_cfg.func("/World/Light", light_cfg)

    self.visualization_markers = define_markers()

    # setting aside useful variables for later
    self.up_dir = torch.tensor([0.0, 0.0, 1.0]).cuda()
    self.yaws = torch.zeros((self.cfg.scene.num_envs, 1)).cuda()
    self.commands = torch.randn((self.cfg.scene.num_envs, 3)).cuda()
    self.commands[:,-1] = 0.0
    self.commands = self.commands/torch.linalg.norm(self.commands, dim=1, keepdim=True)

    # offsets to account for atan range and keep things on [-pi, pi]
    ratio = self.commands[:,1]/(self.commands[:,0]+1E-8)
    gzero = torch.where(self.commands > 0, True, False)
    lzero = torch.where(self.commands < 0, True, False)
    plus = lzero[:,0]*gzero[:,1]
    minus = lzero[:,0]*lzero[:,1]
    offsets = torch.pi*plus - torch.pi*minus
    self.yaws = torch.atan(ratio).reshape(-1,1) + offsets.reshape(-1,1)

    self.marker_locations = torch.zeros((self.cfg.scene.num_envs, 3)).cuda()
    self.marker_offset = torch.zeros((self.cfg.scene.num_envs, 3)).cuda()
    self.marker_offset[:,-1] = 0.5
    self.forward_marker_orientations = torch.zeros((self.cfg.scene.num_envs, 4)).cuda()
    self.command_marker_orientations = torch.zeros((self.cfg.scene.num_envs, 4)).cuda()
```

quat_calc

6. Next we have the method for actually visualizing the markers. Remember, these markers aren’t scene entities! We need to “draw” them whenever we want to see them.

```python
def _visualize_markers(self):
    # get marker locations and orientations
    self.marker_locations = self.robot.data.root_pos_w
    self.forward_marker_orientations = self.robot.data.root_quat_w
    self.command_marker_orientations = math_utils.quat_from_angle_axis(self.yaws, self.up_dir).squeeze()

    # offset markers so they are above the jetbot
    loc = self.marker_locations + self.marker_offset
    loc = torch.vstack((loc, loc))
    rots = torch.vstack((self.forward_marker_orientations, self.command_marker_orientations))

    # render the markers
    all_envs = torch.arange(self.cfg.scene.num_envs)
    indices = torch.hstack((torch.zeros_like(all_envs), torch.ones_like(all_envs)))
    self.visualization_markers.visualize(loc, rots, marker_indices=indices)
```

7. See result for now: `python scripts\reinforcement_learning\skrl\train.py --task=Isaac-Jetbot-Controller-Direct-v0`

8. Observations

```python
def _get_observations(self) -> dict:
    self.velocity = self.robot.data.root_com_vel_w
    self.forwards = math_utils.quat_apply(self.robot.data.root_link_quat_w, self.robot.data.FORWARD_VEC_B)
    obs = torch.hstack((self.velocity, self.commands))
    observations = {"policy": obs}
    return observations
```

9. Reward (When the robot is behaving as desired, it will be driving at full speed in the direction of the command. If we reward both “driving forward” and “alignment to the command”, then maximizing that combined signal)

```python
def _get_rewards(self) -> torch.Tensor:
    forward_reward = self.robot.data.root_com_lin_vel_b[:,0].reshape(-1,1)
    alignment_reward = torch.sum(self.forwards * self.commands, dim=-1, keepdim=True)
    total_reward = forward_reward + alignment_reward
    return total_reward
```

10. Test this setup: `python scripts\reinforcement_learning\skrl\train.py --task=Isaac-Jetbot-Controller-Direct-v0`

11. **Reward and Observation Tuning**

    a. keep the observation space as small as possible (reduce the number parameters & training time) 
    b. reduce and simplify the reward function as much as possible

    **SO**: encode our alignment to the command and our forward speed.

12. New observations

```python
def _get_observations(self) -> dict:
    self.velocity = self.robot.data.root_com_vel_w
    self.forwards = math_utils.quat_apply(self.robot.data.root_link_quat_w, self.robot.data.FORWARD_VEC_B)

    dot = torch.sum(self.forwards * self.commands, dim=-1, keepdim=True)
    cross = torch.cross(self.forwards, self.commands, dim=-1)[:,-1].reshape(-1,1)
    forward_speed = self.robot.data.root_com_lin_vel_b[:,0].reshape(-1,1)
    obs = torch.hstack((dot, cross, forward_speed))

    observations = {"policy": obs}
    return observations
```

13. The dot or inner product tells us how aligned two vectors are as a single scalar quantity

    **SO**: 
        
        Before: we are rewarding driving forward and being aligned to the command by adding them together, so our agent can be reward for driving forward OR being aligned to the command.

        Now: learn to drive in the direction of the command, we should only reward the agent driving forward AND being aligned. Logical AND suggests multiplication and therefore the following reward function:

14. New reward function

```python
def _get_rewards(self) -> torch.Tensor:
    forward_reward = self.robot.data.root_com_lin_vel_b[:,0].reshape(-1,1)
    alignment_reward = torch.sum(self.forwards * self.commands, dim=-1, keepdim=True)
    total_reward = forward_reward*alignment_reward
    return total_reward
```

15. Jetbots have learned to drive in reverse if the command is pointed behind them. (degenerate solutions)
16. New reward to avoid neg *neg = positive rewards but bad behavior

```python
def _get_rewards(self) -> torch.Tensor:
    forward_reward = self.robot.data.root_com_lin_vel_b[:,0].reshape(-1,1)
    alignment_reward = torch.sum(self.forwards * self.commands, dim=-1, keepdim=True)
    total_reward = forward_reward*torch.exp(alignment_reward)
    return total_reward
```

10. Train: `python scripts\reinforcement_learning\skrl\train.py --task=Isaac-Jetbot-Controller-Direct-v0`
11. Play: `python scripts\reinforcement_learning\skrl\play.py --task=Isaac-Jetbot-Controller-Direct-v0`

result

</details>

## Train Flags

```python
# add argparse arguments
parser = argparse.ArgumentParser(description="Train an RL agent with Stable-Baselines3.")
parser.add_argument("--video", action="store_true", default=False, help="Record videos during training.")
parser.add_argument("--video_length", type=int, default=200, help="Length of the recorded video (in steps).")
parser.add_argument("--video_interval", type=int, default=2000, help="Interval between video recordings (in steps).")
parser.add_argument("--num_envs", type=int, default=None, help="Number of environments to simulate.")
parser.add_argument("--task", type=str, default=None, help="Name of the task.")
parser.add_argument("--seed", type=int, default=None, help="Seed used for the environment")
parser.add_argument("--log_interval", type=int, default=100_000, help="Log data every n timesteps.")
parser.add_argument("--checkpoint", type=str, default=None, help="Continue the training from checkpoint.")
parser.add_argument("--max_iterations", type=int, default=None, help="RL Policy training iterations.")
```

`python scripts\reinforcement_learning\skrl\train.py --task=Isaac-Jetbot-Controller-Direct-v0` or `isaaclab.bat scripts\reinforcement_learning\skrl\train.py --task=Isaac-Jetbot-Controller-Direct-v0` or (RANDOM AGENT) `./isaaclab.sh -p scripts/environments/random_agent.py --task Isaac-Cartpole-v0 --num_envs 32`

- Add number of environments to train in parallel: `--num_envs 10`
- Add training mode: 

    - `--headless` (simulation is not rendered during training)
    - `--num_envs 64 --headless --video`: `--enable_cameras` which enables off-screen rendering. Additionally, we pass the flag `--video` which records a video of the agent’s behavior during training. (The videos are saved to the `logs/sb3/Isaac-Cartpole-v0/<run-dir>/videos/train directory`.)
    - ignore the `--headless` to see the simulation rendered in a window and manipulate it (slow down the training process since the simulation is rendered on the screen)

- Play with last checkpoint: `python scripts\reinforcement_learning\skrl\play.py --task=Isaac-Jetbot-Controller-Direct-v0 --num_envs 32 --use_last_checkpoint` (You can also specify a specific checkpoint by passing the `--checkpoint` flag)

EXAMPLE:

`isaaclab.bat -p scripts/reinforcement_learning/rsl_rl/train.py --task Isaac-Velocity-Rough-H1-v0 --headless`

`isaaclab.bat -p scripts/reinforcement_learning/rsl_rl/play.py --task Isaac-Velocity-Rough-H1-v0 --num_envs 64 --checkpoint logs/rsl_rl/h1_rough/EXPERIMENT_NAME/POLICY_FILE.pt`

`isaaclab.bat -p scripts/tutorials/03_envs/policy_inference_in_usd.py --checkpoint logs/rsl_rl/h1_rough/EXPERIMENT_NAME/exported/policy.pt`

<br>

<br>

### BOTZO RL TEMPLATE

I created my own project using Isaac Lab template: [Botzo Template](https://github.com/GRINGOLOCO7/IsaacLab/tree/main/source/isaaclab_tasks/isaaclab_tasks/direct/botzo)

```shell
./isaaclab.sh --new

(env_isaaclab) C:\Users\grego\Desktop\GRINGO\IsaacLab\IsaacLab>python -m pip install -e source\isaaclab_tasks

(env_isaaclab) C:\Users\grego\Desktop\GRINGO\IsaacLab\IsaacLab>python scripts\environments\list_envs.py
```
Result: 
`|   7    | Isaac-Botzo-Direct-v0                                         | isaaclab_tasks.direct.botzo.botzo_env:BotzoEnv                                                        | isaaclab_tasks.direct.botzo.botzo_env_cfg:BotzoEnvCfg`

Now I can use my environment to train:
```shell
(env_isaaclab) C:\Users\grego\Desktop\GRINGO\IsaacLab\IsaacLab>python scripts\reinforcement_learning\skrl\train.py --task=Isaac-Botzo-Direct-v0
```

by default, this should start a cartpole training environment.

Let the training finish and then run the following command to see the trained policy in action!

```shell
python scripts\reinforcement_learning\skrl\play.py --task=Isaac-Botzo-Direct-v0
```

Notice that you did not need to specify the path for the checkpoint file! This is because Isaac Lab handles much of the minute details like checkpoint saving, loading, and logging. In this case, the train.py script will create two directories: logs and output, which are used as the default output directories for tasks run by this project.

"""
1. (env_isaaclab) C:\Users\grego\Desktop\GRINGO\IsaacLab\IsaacLab>   python scripts\environments\list_envs.py
|   3    | Isaac-Velocity-Flat-Anymal-C-Direct-v0           | isaaclab_tasks.direct.anymal_c.anymal_c_env:AnymalCEnv    | isaaclab_tasks.direct.anymal_c.anymal_c_env_cfg:AnymalCFlatEnvCfg                                                                                         |
|   4    | Isaac-Velocity-Rough-Anymal-C-Direct-v0          | isaaclab_tasks.direct.anymal_c.anymal_c_env:AnymalCEnv    | isaaclab_tasks.direct.anymal_c.anymal_c_env_cfg:AnymalCRoughEnvCfg  

2. (env_isaaclab) C:\Users\grego\Desktop\GRINGO\IsaacLab\IsaacLab>   python scripts\reinforcement_learning\skrl\train.py --task Isaac-Velocity-Flat-Anymal-C-Direct-v0
3. (env_isaaclab) C:\Users\grego\Desktop\GRINGO\IsaacLab\IsaacLab>   python scripts\reinforcement_learning\skrl\play.py --task Isaac-Velocity-Flat-Anymal-C-Direct-v0
"""

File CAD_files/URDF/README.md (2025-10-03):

<div align="center">
<h1>BOTZO 🐾</h1>

**`The good boy quadruped robot :)`**

<p align="center">
    <a href="https://www.instagram.com/botzo.ie/" target="_blank" rel="noopener noreferrer">
        
    </a>
    <a href="" target="_blank" rel="noopener noreferrer">
        
    </a>
    <a href="mailto:botzoteam@gmail.com">
        
    </a>
    <a href="">
        
    </a>

more about botzo [here](https://github.com/IERoboticsAILab/botzo)

for specific URDF documentation [here](https://ieroboticsailab.github.io/botzo/build/cad/urdf/)

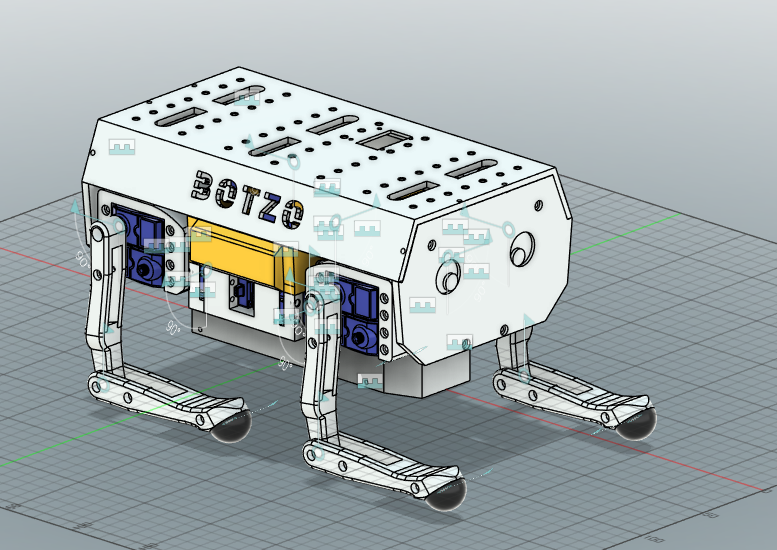
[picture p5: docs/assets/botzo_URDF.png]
botzo


</p>
</div>

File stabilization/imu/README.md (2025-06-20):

<div align="center">
<h1>BOTZO 🐾</h1>

**`The good boy quadruped robot :)`**

<p align="center">
    <a href="https://www.instagram.com/botzo.ie/" target="_blank" rel="noopener noreferrer">
        
    </a>
    <a href="" target="_blank" rel="noopener noreferrer">
        
    </a>
    <a href="mailto:botzoteam@gmail.com">
        
    </a>
    <a href="">
        
    </a>

</p>

</div>

more [here](https://github.com/IERoboticsAILab/botzo)

# IMU_readings
Set up MPU6050 and read rotations and accellerations in each axes

## MPU6050

This sensor is an accellerometer gyroscope. It means it is able to read rotation (roll, pitch, yaw) and accelleration in each axes.

## Usage

After small calibration using build in scripts in `<MPU6050_light.h>` library we where able to test the reading with a simple project translating roll andle in to angles for the servo motor.

### Result

https://github.com/botzo-team/our_images_and_videos/blob/main/IMU_proof_concept.mp4

result

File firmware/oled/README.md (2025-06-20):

<div align="center">
<h1>BOTZO 🐾</h1>

**`The good boy quadruped robot :)`**

<p align="center">
    <a href="https://www.instagram.com/botzo.ie/" target="_blank" rel="noopener noreferrer">
        
    </a>
    <a href="" target="_blank" rel="noopener noreferrer">
        
    </a>
    <a href="mailto:botzoteam@gmail.com">
        
    </a>
    <a href="">
        
    </a>

</p>

</div>

# Result

https://github.com/IERoboticsAILab/botzo_media/blob/main/botzo%20startup%20animation%20vid.gif



For the OLED Display we are using the SH1106 I2C arduino oled display.

## Setup

First thing to do is set up the display with an Arduino UNO: Connect VDD to 5V, GND to GND, SCK to A5, SDA to A4. 

| **SH1106 OLED Pin** | **Arduino UNO Pin** |
|---|---|
| **VCC** | **5V** |
| **GND** | **GND** |
| **SDA** | **A4** |
| **SCL** | **A5** |

In our case the UNO wasn't working but I believe this is an issue to do with the specific board I had, so an UNO should be fine. In case you use a Mega board like I had to, you can connect the wires like this:

| **SH1106 OLED Pin** | **Arduino Mega Pin** |
|---|---|
| **VCC** | **5V** |
| **GND** | **GND** |
| **SDA** | **SDA (Pin 20)** |
| **SCL** | **SCL (Pin 21)** |

## Prerequisites
For this script I used the U8g2 library which handles the display drivers for SH1106. This and Wire.h are enough to handle creating the animation. On top of this I obviously needed an animation, so I used the Aseprite software to make a simple white on black pixel animation, matching the 128x64 px resolution of the display. 

Make sure to save each frame of the animation in .bmp so that you have a bitmap file (this makes it easier for the next process to be done) but .png works too. Last thing we need before we actually write the code for the animation is to convert our bitmap files into code that can be displayed on the display. To do this I uploaded the .bmp files onto [this](https://javl.github.io/image2cpp/) website with the following settings:

- **Output Format:** Monochrome
- **Byte Orientation:** Horizontal
- **Size:** 128x64 (or whatever matches your display's resolution)

The website will output a bitmap code that translates the pixels on each of your animation's frames into something that is readable by the arduino, like this:

``` cpp

// 'Sprite-0001', 128x64px
const unsigned char myBitmapSprite_0001 [] PROGMEM = {
	0x00, 0x00, 0x00, 0x00, 0x00, 0x00, 0x00, 0x00, 0x00, 0x00, 0x00, 0x00, 0x00, 0x00, 0x00, 0x00, 
	0x00, 0x00, 0x00, 0x00, 0x00, 0x00, 0x00, 0x00, 0x00, 0x00, 0x00, 0x00, 0x00, 0x00, 0x00, 0x00, 
	0x00, 0x00, 0x00, 0x00, 0x00, 0x00, 0x00, 0x00, 0x00, 0x00, 0x00, 0x00, 0x00, 0x00, 0x00, 0x00, 
	0x00, 0x00, 0x00, 0x00, 0x00, 0x00, 0x00, 0x00, 0x00, 0x00, 0x00, 0x00, 0x00, 0x00, 0x00, 0x00, 
	0x00, 0x00, 0x00, 0x00, 0x00, 0x00, 0x00, 0x00, 0x00, 0x00, 0x00, 0x00, 0x00, 0x00, 0x00, 0x00, 
	0x00, 0x00, 0x00, 0x00, 0x00, 0x00, 0x00, 0x00, 0x00, 0x00, 0x00, 0x00, 0x00, 0x00, 0x00, 0x00, 
	0x00, 0x00, 0x00, 0x00, 0x00, 0x00, 0x00, 0x00, 0x00, 0x00, 0x00, 0x00, 0x00, 0x00, 0x00, 0x00, 
	0x00, 0x00, 0x00, 0x00, 0x00, 0x00, 0x00, 0x00, 0x00, 0x00, 0x00, 0x00, 0x00, 0x00, 0x00, 0x00, 
	0x00, 0x00, 0x00, 0x00, 0x00, 0x00, 0x00, 0x00, 0x00, 0x00, 0x00, 0x00, 0x00, 0x00, 0x00, 0x00, 
	0x00, 0x00, 0x00, 0x00, 0x00, 0x00, 0x00, 0x00, 0x00, 0x00, 0x00, 0x00, 0x00, 0x00, 0x00, 0x00, 
	0x00, 0x00, 0x00, 0x00, 0x00, 0x00, 0x00, 0x00, 0x00, 0x00, 0x00, 0x00, 0x00, 0x00, 0x00, 0x00, 
	0x00, 0x00, 0x00, 0x00, 0x00, 0x00, 0x00, 0x00, 0x00, 0x00, 0x00, 0x00, 0x00, 0x00, 0x00, 0x00, 
	0x00, 0x00, 0x00, 0x00, 0x00, 0x00, 0x00, 0x00, 0x00, 0x00, 0x00, 0x00, 0x00, 0x00, 0x00, 0x00, 
	0x00, 0x00, 0x00, 0x00, 0x00, 0x00, 0x00, 0x00, 0x00, 0x00, 0x00, 0x00, 0x00, 0x00, 0x00, 0x00, 
	0x00, 0x00, 0x00, 0x00, 0x00, 0x00, 0x00, 0x00, 0x00, 0x00, 0x00, 0x00, 0x00, 0x00, 0x00, 0x00, 
	0x00, 0x00, 0x00, 0x00, 0x00, 0x00, 0x00, 0x00, 0x00, 0x00, 0x00, 0x00, 0x00, 0x00, 0x00, 0x00, 
	0x00, 0x00, 0x00, 0x00, 0x00, 0x00, 0x00, 0x00, 0x00, 0x00, 0x00, 0x00, 0x00, 0x00, 0x00, 0x00, 
	0x00, 0x00, 0x00, 0x00, 0x00, 0x00, 0x00, 0x14, 0x00, 0x00, 0x00, 0x00, 0x00, 0x00, 0x00, 0x00, 
	0x00, 0x00, 0x00, 0x00, 0x00, 0x00, 0x00, 0x2a, 0x00, 0x00, 0x00, 0x00, 0x00, 0x00, 0x00, 0x00, 
	0x00, 0x00, 0x00, 0x00, 0x00, 0x00, 0x00, 0x08, 0x00, 0x00, 0x00, 0x00, 0x00, 0x00, 0x00, 0x00, 
	0x00, 0x00, 0x00, 0x00, 0x00, 0x00, 0x00, 0x7f, 0x00, 0x00, 0x00, 0x00, 0x00, 0x00, 0x00, 0x00, 
	0x00, 0x00, 0x00, 0x00, 0x00, 0x00, 0x80, 0x80, 0x00, 0x00, 0x00, 0x00, 0x00, 0x00, 0x00, 0x00, 
	0x00, 0x00, 0x00, 0x00, 0x00, 0x00, 0x40, 0x00, 0x01, 0x00, 0x00, 0x00, 0x00, 0x00, 0x00, 0x00, 
	0x00, 0x00, 0x00, 0x00, 0x00, 0x00, 0x40, 0x00, 0x01, 0x00, 0x00, 0x00, 0x00, 0x00, 0x00, 0x00, 
	0x00, 0x00, 0x00, 0x00, 0x00, 0x00, 0x4c, 0x00, 0x19, 0x00, 0x00, 0x00, 0x00, 0x00, 0x00, 0x00, 
	0x00, 0x00, 0x00, 0x00, 0x00, 0x00, 0x32, 0x00, 0x26, 0x00, 0x00, 0x00, 0x00, 0x00, 0x00, 0x00, 
	0x00, 0x00, 0x00, 0x00, 0x00, 0x00, 0x21, 0x00, 0x42, 0x00, 0x00, 0x00, 0x00, 0x00, 0x00, 0x00, 
	0x00, 0x00, 0x00, 0x00, 0x00, 0x80, 0x20, 0x77, 0x82, 0x00, 0x00, 0x00, 0x00, 0x00, 0x00, 0x00, 
	0x00, 0x00, 0x00, 0x00, 0x00, 0x40, 0xb8, 0x94, 0x0e, 0x01, 0x00, 0x00, 0x00, 0x00, 0x00, 0x00, 
	0x00, 0x00, 0x00, 0x00, 0x00, 0x40, 0xa4, 0x94, 0x12, 0x01, 0x00, 0x00, 0x00, 0x00, 0x00, 0x00, 
	0x00, 0x00, 0x00, 0x00, 0x00, 0x40, 0xa2, 0xb6, 0x22, 0x01, 0x00, 0x00, 0x00, 0x00, 0x00, 0x00, 
	0x00, 0x00, 0x00, 0x00, 0x00, 0x40, 0xa2, 0xb6, 0x22, 0x01, 0x00, 0x00, 0x00, 0x00, 0x00, 0x00, 
	0x00, 0x00, 0x00, 0x00, 0x00, 0x40, 0xa2, 0x94, 0x22, 0x01, 0x00, 0x00, 0x00, 0x00, 0x00, 0x00, 
	0x00, 0x00, 0x00, 0x00, 0x00, 0xc0, 0xe1, 0xff, 0xc3, 0x01, 0x00, 0x00, 0x00, 0x00, 0x00, 0x00, 
	0x00, 0x00, 0x00, 0x00, 0x00, 0x00, 0x18, 0x08, 0x0c, 0x00, 0x00, 0x00, 0x00, 0x00, 0x00, 0x00, 
	0x00, 0x00, 0x00, 0x00, 0x00, 0x00, 0x08, 0x1c, 0x08, 0x00, 0x00, 0x00, 0x00, 0x00, 0x00, 0x00, 
	0x00, 0x00, 0x00, 0x00, 0x00, 0x00, 0x04, 0x1c, 0x10, 0x00, 0x00, 0x00, 0x00, 0x00, 0x00, 0x00, 
	0x00, 0x00, 0x00, 0x00, 0x00, 0x00, 0x04, 0x1c, 0x10, 0x00, 0x00, 0x00, 0x00, 0x00, 0x00, 0x00, 
	0x00, 0x00, 0x00, 0x00, 0x00, 0x00, 0x04, 0x08, 0x10, 0x00, 0x00, 0x00, 0x00, 0x00, 0x00, 0x00, 
	0x00, 0x00, 0x00, 0x00, 0x00, 0x00, 0x02, 0x08, 0x20, 0x00, 0x00, 0x00, 0x00, 0x00, 0x00, 0x00, 
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
};
```

I know it looks scary but this is just an array where every element is a pixel on the screen, so this one has 8192 elements (128 * 64). The code above is the first frame of our animation (the one I pasted above on the gif). Since this is a huge piece of code I put each frame into their own .h file to make it easier to navigate and then imported each file into the main script, but you can also put them all in one .h file and only import that.

Once all these steps are done here are all my imports at the start of the script:

``` cpp

#include <Wire.h>
#include <U8g2lib.h>
#include "frame1.h"
#include "frame2.h"
#include "frame3.h"
#include "frame4.h"
#include "frame5.h"
#include "frame6.h"
#include "frame7.h"
#include "frame8.h"
#include "frame9.h"
#include "frame10.h"
#include "frame11.h"
#include "frame12.h"

```

## Main code

Once we've imported all the frames as well as the necessary libraries, you can initialize your display with the following line: `U8G2_SH1106_128X64_NONAME_F_HW_I2C u8g2(U8G2_R0, /* reset=*/ U8X8_PIN_NONE, 0x60);`.
The one thing to watch out for here is the `0x60`, as this is your Arduino board's address and it varies from model to model and sometimes even between individual boards (the most common is 0x3C). You can find out your board's address by pasting the code on (this)[https://playground.arduino.cc/Main/I2cScanner/] page and checking your serial monitor. 

### Assigning variables

We create an array that holds pointers all frames so that we can loop through them as needed, like this:

``` cpp
const unsigned char* frames[] = {
    myBitmapSprite_0001, myBitmapSprite_0002, myBitmapSprite_0003, 
    myBitmapSprite_0004, myBitmapSprite_0005, myBitmapSprite_0006, 
    myBitmapSprite_0007, myBitmapSprite_0008, myBitmapSprite_0009, 
    myBitmapSprite_0010, myBitmapSprite_0011, myBitmapSprite_0012
};
```

Then we assign the following variables:

``` cpp
const int frameCount = 12;
const int maxLoops = 5;
int loopCounter = 0;
```

This is very simple. The first one (`frameCount`) is obviously just keeping how many frames our animation has. This will be useful for looping through each frame to create a coherent animation later. The second one (`MaxLoops`) defines how many times over the animation will play. I made it play a limited number of times because when I tried using a while true loop after some point the animation would freeze, likely caused by an overflow issue that I haven't looked into yet. the final variable (`loopCounter`) is, again, very obviously to keep track of which iteration of the loop we are in.

### Setting up the display

To start the display up we run two simple lines of code in the setup function from the Arduino IDE:

```cpp
void setup() {
    u8g2.setI2CAddress(0x60 * 2);  // Set correct I2C address
    u8g2.begin();
}
```

The first line ensures that we have set up the correct board address (to find your board's address refer to the website mentioned above or look for an I2C scanner yourself). The reason we multiply the address by 2 is because U8g2 requires an 8-bit address so this is how we convert it. The next line just initializes the OLED display and sets up communication with the board.

### Running the animation

Finally, we finish off by running the animation. The way to do this is very simple, we first run an if statement checking how many times we have already looped through the animation, and if it is lower than the `maxLoops` variable we set, it runs the animation. Otherwise, it stops the animation at the last frame. Here is the entire loop function:

``` cpp
void loop() {
    if (loopCounter < maxLoops) {
        for (int i = 0; i < frameCount; i++) {
            u8g2.clearBuffer();
            u8g2.drawXBMP(0, 0, 128, 64, frames[i]);
            u8g2.sendBuffer();
            delay(100);
        }
        loopCounter++;
    } else {
        u8g2.clearBuffer();
        u8g2.drawXBMP(0, 0, 128, 64, frames[frameCount - 1]);
        u8g2.sendBuffer();
        while (1);
    }
}
```

As you can see this is very simple and straightforward. The functions used in each loop are all from the library we imported in the beginning, and the two main ones are `drawXBMP()`, which draws the BMP code onto the screen (obtained from the array above) and the `clearBuffer()`/`sendBuffer()` functions, which clear the memory (preventing flickering or leftover pixels from the last frame) and update the display, respectively.

The next steps are to calculate battery information from botzo and display them on the screen :)

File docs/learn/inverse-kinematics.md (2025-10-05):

# Inverse Kinematics

Inverse Kinematics (IK) is a mathematical approach used in robotics to determine the necessary joint angles to position an end-effector (like a robotic arm or leg) at a specific point in space. This is particularly useful for robots with multiple degrees of freedom (DoF), such as our botzo v2s, which has 3 DoF per leg.

Inverse Kinematics is used in robots with legs or arms. It is a series of matrix moltiplications and trigonometry formulas (sin, cos,atan2 law of cosin, pitagora, etc...), in order too find the angles each motor in the leg need to have to reach a point in space (x,y,z). Our dog have 3 Degrees of freedom (3DoF), meaning 3 motors per leg.

_On the other side forward kinematics calculate where the end-effector/the foot end up based on given/known angles of each motor._

Both uses known constants such as lenght of each "bone". For Inverse Kinematic also the target point is a known variable, and it allow us to find the angle configuration we need to reach that point in space.

IK3DOF

firststeps

!!! note

    In `coordinates_to_servos.ipynb` we have combined the use of our IK with the transformation from degrees to PWM explained in [calibrate servos repo](https://github.com/IERoboticsAILab/botzo/tree/main/control/inverse_kinematics/servo_calibration)

## 3 DoF IK Of 1 leg

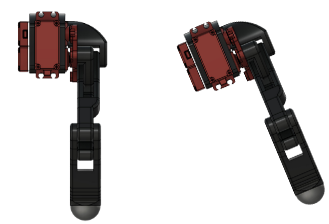
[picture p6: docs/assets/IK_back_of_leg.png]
IK_back_of_leg


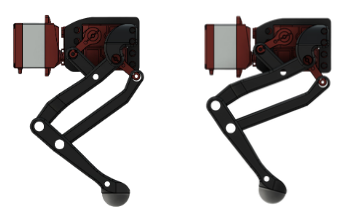
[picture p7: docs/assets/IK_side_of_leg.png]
IK_side_of_leg


### Solver

Note:

```
coxa = A = 3.1 cm
femur = E = 9.5 cm
real_femur = E' = 9.1 cm
tibia = F = 9.8 cm
θ(coxa) = ψ
θ(knee) = Φ
θ(shoulder) = θ
dist_focuspoint_servo_femurtibia = 2.8 cm
X, Y, Z = given target point
```

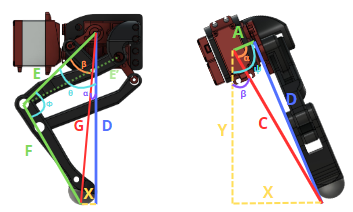
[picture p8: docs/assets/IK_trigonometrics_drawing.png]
IK_trigonometrics_drawing


1. Distance Calculation

```math
D = \sqrt{Z^2 + Y^2 - \text{A}^2}
```

2. G Calculation

```math
G = \sqrt{D^2 + X^2}
```

3. Knee Angle

```math
\text{Φ} = \arccos\left(\frac{G^2 - \text{E}^2 - \text{F}^2}{-2 \cdot \text{E} \cdot \text{F}}\right)
```

4. Shoulder Angle

```math
\theta_{\text{shoulder}} = \arctan2(X, D) + \arcsin\left(\frac{\text{F} \cdot \sin(\text{Φ})}{G}\right)
```

5. Coxa Angle

```math
\text{ψ} = \arctan2(Y, Z) + \arctan2(D, \text{A})
```

### Translator

Here we will translate the founded angles with the translator in the actual angles we will pass to the robot servos

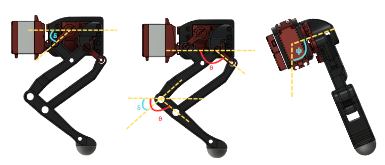
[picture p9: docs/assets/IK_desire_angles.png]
IK_desire_angles


1. Adjustment

```math
\text{adjustment} = \arccos\left(\frac{\text{real\_femur}^2 + \text{femur}^2 - \text{dist\_focuspoint\_servo\_femurtibia}^2}{2 \cdot \text{real\_femur} \cdot \text{femur}}\right)
```

2. Femur Angle

```math
\theta_{\text{femur}} = \frac{\pi}{2} - (\theta_{\text{shoulder}} + \text{adjustment})
```

3. Tibia Angle

```math
\theta_{\text{tibia}} = \pi - \theta_{\text{knee}} + \text{adjustment} + \theta_{\text{femur}}
```

### Resources

[Spot-Micro](https://spotmicroai.readthedocs.io/en/latest/simulation/)

  - [Spot-Micro GitHub](https://gitlab.com/public-open-source/spotmicroai/simulation/-/tree/master/Basic%20simulation%20by%20user%20Florian%20Wilk/Kinematics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)

  - [Spot-Micro IK solver video](https://www.youtube.com/watch?v=4rc8N1xuWvc)

[OpenQuadruped/spot_mini_mini](https://github.com/OpenQuadruped/spot_mini_mini)

## Rotation Matrices

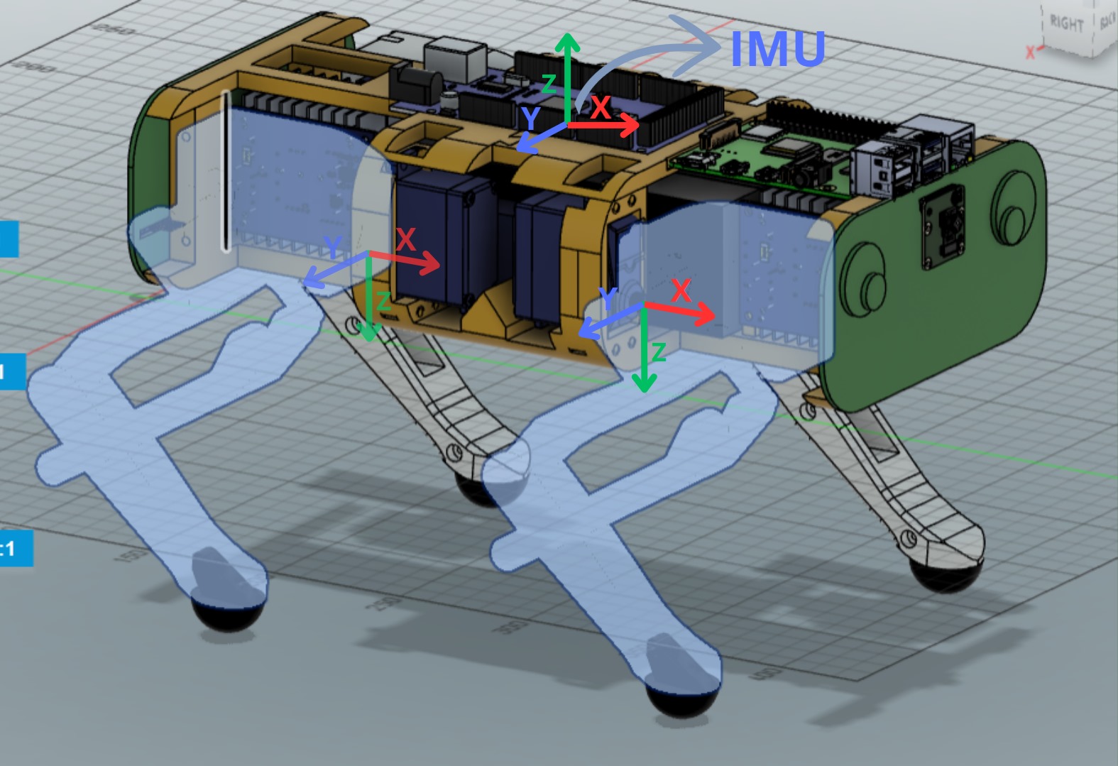
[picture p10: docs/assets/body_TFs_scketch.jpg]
body_TFs_scketch


!!! note

    Rotation matrices repo: [here](https://github.com/IERoboticsAILab/botzo/tree/main/control/rotation_matrices)

    Rotation matrices docs: [here](https://ieroboticsailab.github.io/botzo/learn/rotation-matrices/)

## IK full body

Use `IK_solver4Lgs.ipynb`. It is a way to manualy retrive angles for each leg to make robot step and walking for the first time.

1. First the code loads known variables, such as the coefficents retrived from the calibration of each servo (find more [here](https://github.com/IERoboticsAILab/botzo/tree/main/control/inverse_kinematics/servo_calibration)).

and robot dimentions.

2. We define some usefull function for later (such as translate read to degrees)

3. We craete a IK solver for each leg. The only thing that changes is the adjustemts need for each leg servo angle. Because some servos has diffrent orientation therfor diffrent zero.

4. Then we manualy define points in the 3D space (x,y,z) inside an array. This points will then later be passed one by one to the IK solvers adn we will return PWM signals for the corrisponding angle that each servo need to have to reach that point.
  - Each leg has his own IK solver, given the fact that the motors are oriented in diffrent ways.
  - Differences from Front to Back: Just in the shoulder angle, infact the servo is oriented on the opposite side. So we just do `180° - angle_in_right`

  *FR*

  ```python
  coxa_angle = deg2rad(180) - (np.arctan2(y,z) + np.arctan2(D,coxa))
  ```

  *BR*
  ```python
  coxa_angle = (np.arctan2(y,z) + np.arctan2(D,coxa))
  ```

  - Differences from Left to Right:

    1. First we have to flip both angles in knee and tibia of about 180°.

    *FR*

    ```python
    femur_angle = deg2rad(90) - (shoulder_angle + adjustment)
    tibia_angle = np.pi - knee_angle + femur_angle + adjustment
    ```

    *FL*

    ```python
    femur_angle = (deg2rad(90) - (shoulder_angle + adjustment))
    tibia_angle = deg2rad(180) - (np.pi - knee_angle + femur_angle + adjustment)
    femur_angle = deg2rad(180) - femur_angle
    ```

    2. We have to change the position of the shoulder. The math think that the shoulder is at the right of the leg, but in the right leg, the shoulder servo is at the left to respect to the leg (indide the robot).

    We want to achive this:

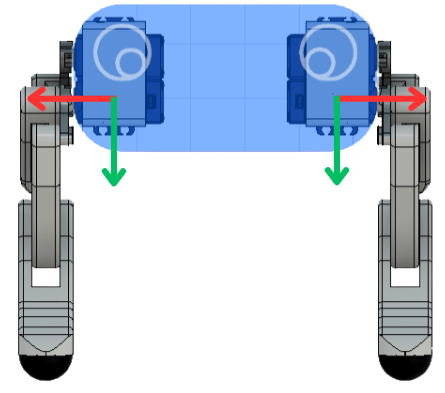
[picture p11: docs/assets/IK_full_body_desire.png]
IK_full_body_desire
    

    But the math make the robot beleve it is in this configuration (where the leg is duplicated, not mirrored):

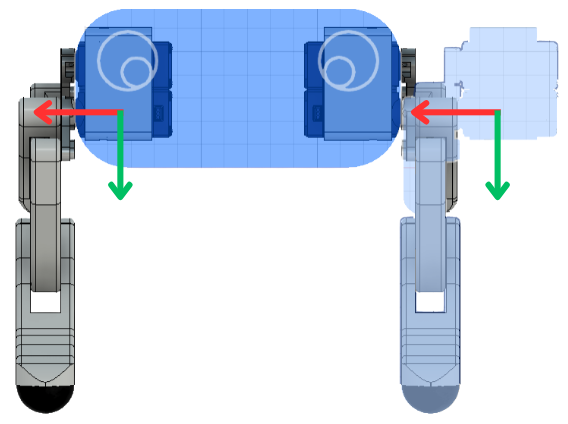
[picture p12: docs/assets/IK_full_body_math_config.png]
IK_full_body_math_config
    

    So the result of IK solver is something like this (not precise, and mooving on a curve rather than a line):

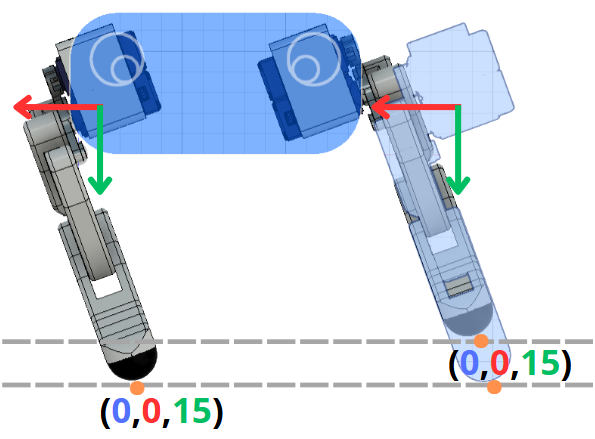
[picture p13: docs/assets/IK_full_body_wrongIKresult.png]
IK_full_body_wrongIKresult
    

    After the flip we end up in the desire configuration (we basically move the shoulder inside the robot. In other words we flip the output angle of the shoulder based on the vertical line):

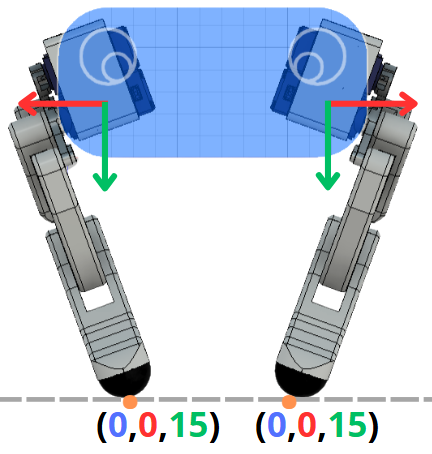
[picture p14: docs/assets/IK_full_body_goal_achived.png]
IK_full_body_goal_achived
    

    *FR*

    ```python
    coxa_angle = deg2rad(180) - (np.arctan2(y,z) + np.arctan2(D,coxa))
    ```

    *FL*

    ```python
    coxa_angle = (deg2rad(180) - (np.arctan2(y,z) + np.arctan2(D,coxa))) - (2 * ((deg2rad(180) - (np.arctan2(y,z) + np.arctan2(D,coxa)))-deg2rad(90)))
    ```

5. We parse the result in a way the we can just copy and paste it in the `test_4legs.ino.ino` arduino code. The arduino code connect to each servo and move them coordinately. So we where able to manualy simulate a Walking Gate. For a more general and sophisticated gate look [here](https://github.com/IERoboticsAILab/botzo/tree/main/control/gait_plan)

firststeps
walking

---

[BOTZO IK REPO](https://github.com/IERoboticsAILab/botzo/tree/main/control/inverse_kinematics)

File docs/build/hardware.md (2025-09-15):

# Hardware

## Overview

Botzo hardware components are aimed at being affordable but still of decent quality.
The components can be summarized by the following 4 types:

- **Processing Unit**: Raspberry Pi 4 (future: Jetson Nano).
- **Actuators**: Optimizing torque for robust movement (25kg servos x3 per leg).
- **Power Supply**: Batteries capable of delivering ~30 minutes of runtime under typical conditions.
- **Sensors**: Integrating components for environmental awareness. Botzo top is universal base for attaching fourther components, such as webcam and LiDAR.

For a deeper dive into this phase, check out our [Canva Board Proposal](https://www.canva.com/design/DAGQqN2k1i4/RCJst_pNSHRcbE02HOKgEw/edit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).

<figure markdown="span">
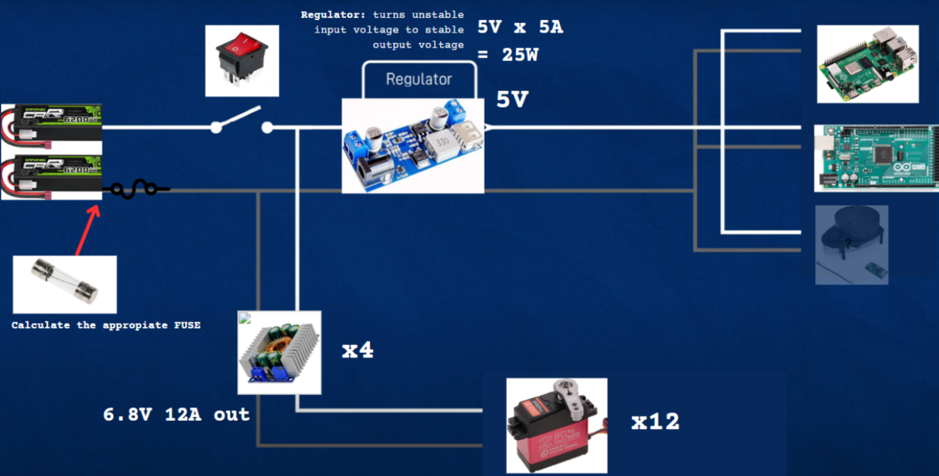
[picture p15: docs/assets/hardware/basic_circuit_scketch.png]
Basic Circuit
    
    <figcaption>Full Circuite Schematic highlighting the connections between components.</figcaption>
</figure>
<figure markdown="span">
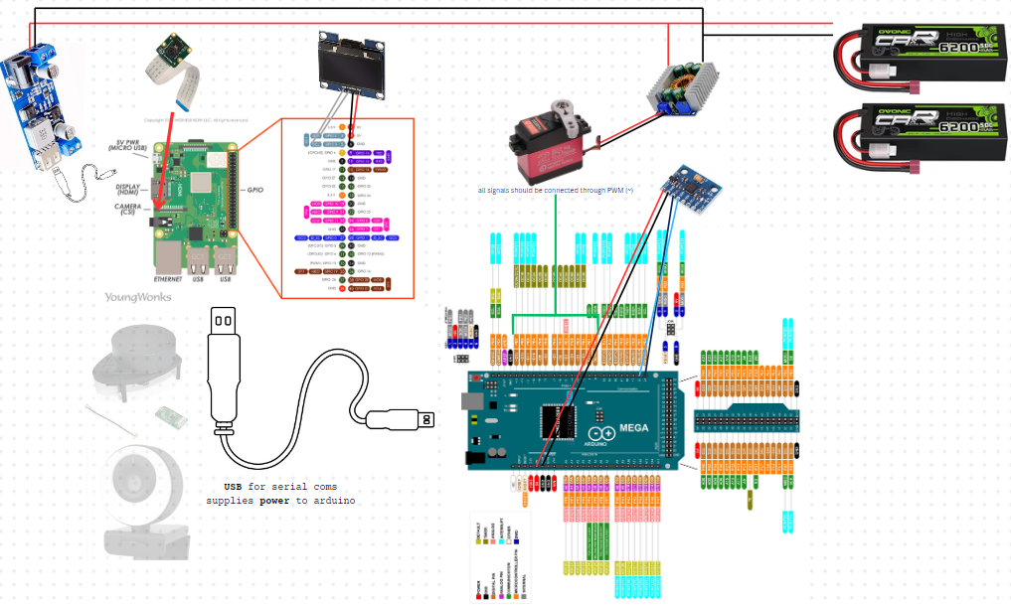
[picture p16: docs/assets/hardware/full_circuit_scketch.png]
Full Circuit
    
    <figcaption>Full Circuite Schematic highlighting the connections between components.</figcaption>
</figure>

## Bill Of Materials

<!-- TODO: Links are missing!
    Additionally, this should not reflect on what items are and aren't available in the lab
    but rather for anyone.
-->

### Electronics

| Component | Link | Price (Single) | Component Total | Description | Quantity |
| --- | --- | --- | --- | --- | --- |
| Arduino Mega | [Amazon](https://www.amazon.com) | 25.99€ | 25.99€ | Control over servos and IMU | x1 |
| Raspberry Pi | - | - | - | Brain | x1 |
| Raspberry Pi camera module V2 8MP | [Amazon](https://www.amazon.com) | 13.79€ | 13.79€ | Camera module for Raspberry | x1 |
| Buck converter 5V-5A out | [Amazon](https://www.amazon.com) | 11.99€ | 11.99€ | Buck converter 5V-5A (25W) for Rpi | x1 |
| Buck converter 5-40V 12A out | [Amazon](https://www.amazon.com) | 35.99€ | 35.99€ | Buck converters for servos | x5 |
| Servo DS3225 25kg | - | - | - | Actuators for legs | x12 |
| MPU-6050 | - | - | - | Balancing sensor | x1 |
| LiPo batteries RC | [Amazon](https://www.amazon.com) | 45.99€ | 91.98€ | Power in series | x2 |
| Oled Display | [Amazon](https://www.amazon.com) | 9.99€ | 9.99€ | Display informations | x1 |
| PS3 controller | [Amazon](https://www.amazon.com) | 17.99€ | 17.99€ | PS3 controller to move robot | x1 |

### Fastners & Materials

| Component | Link | Price (Single) | Component Total | Description | Quantity |
| --- | --- | --- | --- | --- | --- |
| 8x3x4 mm bearings | Amazon | 7.09€ | 14.18€ | Bearings for moving parts  | x20 |
| 10x5x4 mm bearings | Amazon | 7.09€ | 7.09€ | For shoulder stronger axes | x4 |
| Dean T Connectors | Amazon | 9.99€ | 9.99€ | Connection of the circuit  | x1 |
| Cables 14 AWG | Amazon | 25.5€ | 25.5€ | Cables high current | x1 |
| Cables 10 AWG | Amazon | 16.99€ | 16.99€ | Cables high current | x1 |
| TPU filament | Bambu  | 44.73€ | 44.73€ | TPU for foot | x1 |
| PETG filament | Amazon | - | - | TPU for foot | x1 |
| Set of M3, M2.5 and M2 screws | - | - | - | - | - |
| Set of inserts for M3, M2.5 and M2 screws | - | - | - | - | - |

**Total: 256.39€**

_Price can vary depending on what you already have, but the goal is to stay under 500€_

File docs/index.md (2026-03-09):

# 🐕 Botzo {align=center}

<p align="center"><i>A legged robot platform designed to learn by building it!</i></p>

<p align="center">
    <a href="https://www.instagram.com/botzo.ie/" target="_blank" rel="noopener noreferrer">
        
    </a>
    <a href="https://www.youtube.com/@Botzoie" target="_blank" rel="noopener noreferrer">
        
    </a>
    <a href="mailto:botzoteam@gmail.com">
        
    </a>
</p>

---

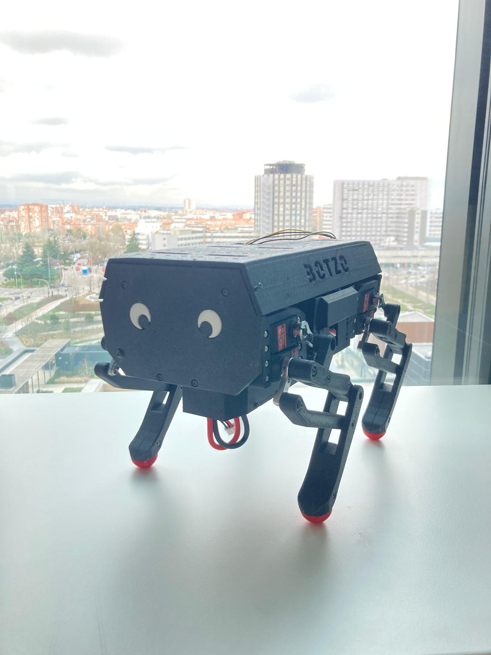
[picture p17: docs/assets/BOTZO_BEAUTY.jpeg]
botzo hero picture


**Botzo** is a legged robot platform which is aimed to help students and enthusiasts in robotics
to simulate, build and program a robot. The project aim is to have a robot that it's cost
should be targeted to be under the 500 euros mark.

Furthermore, due to the nature of a quadruped robot,
this platform should excel at the following:

- Navigate complex terrains
- Collect data and samples
- Interact with its environment

## Project Current State

**This project is still in active development and currently in its early stages.**

So far, the platform has gone through component selection, CAD design and assembly,
and building the inverse kinematics model. It's now in the simulation phase,
where the goal is to use **reinforcement learning** to "teach" Botzo how to walk on its own.

## Why Botzo?

**Botzo** is a legged robot platform designed not just to function, but to teach.
It was created with the goal of helping people learn about robotics by building,
experimenting, and exploring key concepts along the way — from hardware design and
assembly to control systems, simulation, and machine learning.

Unlike many robotics kits that act as black boxes, Botzo is open and modular.
Every part of it — mechanical, electrical, and software — is intended to be a
learning opportunity. Whether you're diving into inverse kinematics or training
locomotion with reinforcement learning, Botzo encourages curiosity and hands-on experimentation.

If you're interested in robotics, simulation, or intelligent locomotion,
Botzo isn't just a project — it's a platform for learning.

---

[BOTZO GITHUB REPO](https://github.com/IERoboticsAILab/botzo)

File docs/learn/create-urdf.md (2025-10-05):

# Generating Botzo URDF

Documentation on how to build our URDF from STL file

A URDF is a file used i robotics to import the robot in a simulation. It uses the STL/CAD files as a base. Assemble them with rigid or rotatory joins, and save positions of each bone and pivot in the joints. To sum up, it is file that describe your robot in deep details and precision.

Download our URDF [here](https://github.com/IERoboticsAILab/botzo/blob/main/CAD_files/URDF/BOTZO_URDF_description/urdf/BOTZO_URDF.urdf)

## Resources

Visit directly the repos if you don't understand something. This is a resume of what they do:

- [Webgraphviz](http://www.webgraphviz.com/)
- [Joint2Graphviz repo zip](https://github.com/yanshil/Joint2Graphviz)
- [Fusion2PyBullet repo zip](https://github.com/yanshil/Fusion2PyBullet)
- [fusion2urdf](https://github.com/syuntoku14/fusion2urdf) <-- deprecated

## Prepare STL

As stated in the [Fusion2PyBullet repo](https://github.com/yanshil/Fusion2PyBullet), we must **prepare our STL** file properly.

1. All bodies/peaces/future links must be **components**.
2. Add physical materials
3. Add **joint** to connect all components. In fusion you can select various type of joint (static, rotational, etc...) and also the pivot point.
4. Call one componet as `base_link`
5. Remove links of comonents (if the are right clik on it and press Break Link)
   Result: https://github.com/IERoboticsAILab/botzo/blob/main/media_assests/fusion_joints_one_leg.mp4
   result
6. Check STL joint-link structure using [Webgraphviz](http://www.webgraphviz.com/). Here how:

   - Download [Joint2Graphviz repo](https://github.com/yanshil/Joint2Graphviz) as a ZIP.
   - Extract the ZIP in a known directory.
   - Open terminal:

     ```powershell
     cd <path to Joint2Graphviz>

     Copy-Item ".\Joint2Graphviz-master\" -Destination "${env:APPDATA\Autodesk\Autodesk Fusion 360\API\Scripts\" -Recurse
     ```

     For me was:

     ```powershell
      cd C:\Users\orlan\OneDrive\Desktop\side_projects\Joint2Graphviz-master

      Copy-Item "..\Joint2Graphviz-master\" -Destination "..\..\..\..\AppData\Roaming\Autodesk\Autodesk Fusion 360\API\Scripts\" -Recurse
     ```

   - Now the script to create a `.txt` file for your link graph is added to fusion
   - Open fusion
   - Open the file of the robot
   - Go to utility > Addins
   - Under `My Script` you should see `Joint2Graphviz`
   - Press it. It will create a `graph.txt`
   - Copy and pase the text content to [Webgraphviz](http://www.webgraphviz.com/) and check your robot tf structure to be valid.

**(for more infors check [Joint2Graphviz readme](https://github.com/yanshil/Joint2Graphviz))**

---

!!! warning

    7. We discovered that URDF does NOT suport close loop. Our leg design is one big close loop. You can check `wrong_graph` folder to see a graph with a close loop... The URDF won't work if there is a close loop

## Export URDF

1. Download [Fusion2PyBullet](https://github.com/yanshil/Fusion2PyBullet) as a ZIP
2. Extract the ZIP in a known directory.
3. Open terminal:

   ```powershell
   cd <path to Fusion2PyBullet>

   Copy-Item ".\URDF_Exporter\" -Destination "${env:APPDATA}\Autodesk\Autodesk Fusion 360\API\Scripts\" -Recurse
   ```

   For me was:

   ```powershell
       PS C:\Users\orlan\OneDrive\Desktop\side_projects\Fusion2PyBullet-master> Copy-Item ".\Bullet_URDF_Exporter\" -Destination "..\..\..\..\AppData\Roaming\Autodesk\Autodesk Fusion 360\API\Scripts\" -Recurse
   ```

4. Open fusion > utils > addins > my scripts > Bullet_URDF_Exporter
5. My URDF [here](https://github.com/IERoboticsAILab/botzo/blob/main/CAD_files/URDF/BOTZO_URDF_description/urdf/BOTZO_URDF.urdf)

**(for more infors check [fusion2urdf readme](https://github.com/syuntoku14/fusion2urdf/blob/master/README.md) or [Fusion2PyBullet readme](https://github.com/yanshil/Fusion2PyBullet/blob/master/README.md))**

---

[BOTZO URDF REPO](https://github.com/IERoboticsAILab/botzo/tree/main/CAD_files/URDF)

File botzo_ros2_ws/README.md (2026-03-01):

<div align="center">
<h1>BOTZO 🐾</h1>

**`The good boy quadruped robot :)`**

<p align="center">
    <a href="https://www.instagram.com/botzo.ie/" target="_blank" rel="noopener noreferrer">
        
    </a>
    <a href="" target="_blank" rel="noopener noreferrer">
        
    </a>
    <a href="mailto:botzoteam@gmail.com">
        
    </a>
    <a href="">
        
    </a>

more about botzo [here](https://github.com/IERoboticsAILab/botzo)

for specific ROS2 botzo workspace documentation [here](https://ieroboticsailab.github.io/botzo/build/software/ros/)

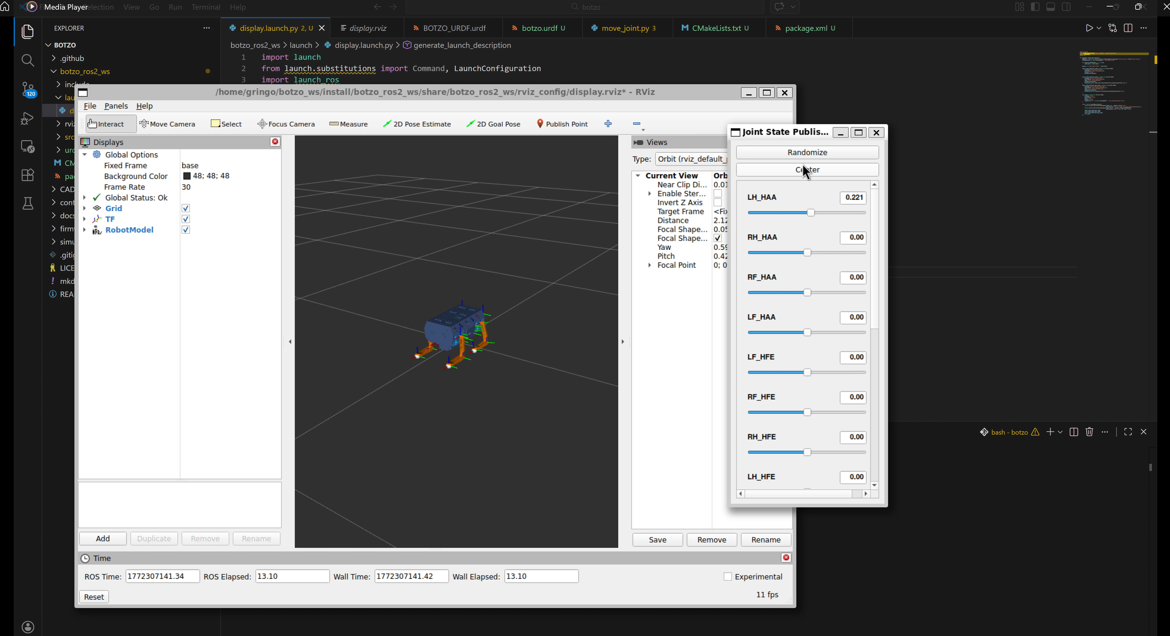
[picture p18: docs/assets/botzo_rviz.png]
results


</p>
</div>

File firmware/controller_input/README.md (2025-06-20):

<div align="center">
<h1>BOTZO 🐾</h1>

**`The good boy quadruped robot :)`**

<p align="center">
    <a href="https://www.instagram.com/botzo.ie/" target="_blank" rel="noopener noreferrer">
        
    </a>
    <a href="" target="_blank" rel="noopener noreferrer">
        
    </a>
    <a href="mailto:botzoteam@gmail.com">
        
    </a>
    <a href="">
        
    </a>

</p>

</div>

more [here](https://github.com/IERoboticsAILab/botzo)

# PS4_Controller_Reading

This repository contains the files associated with developing the software to read and acknowledge inputs from the ps4 controller that will be used to control Botzo.

# Controller Input Layout
Below is the current concept for the associations of each button input from the PS4 controller regarding how Botzo will respond to it.


# UI Interface
A simple UI INterface was designed in order to assess whether the software was accurately reading the inputs of the PS4 controller, ensuring accuracy and success when it is used with Botzo, avoiding errors and reducing the overall chances of future possible complications.

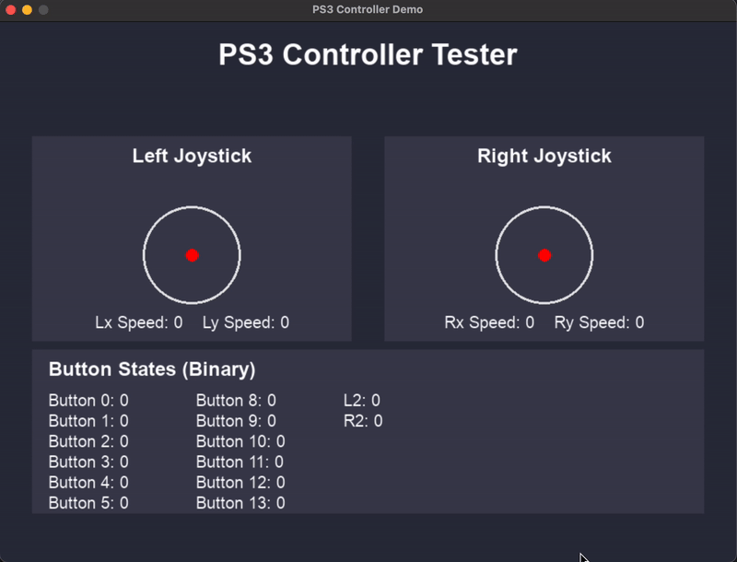
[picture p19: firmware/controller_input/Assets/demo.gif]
Demo


https://www.padcrafter.com/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

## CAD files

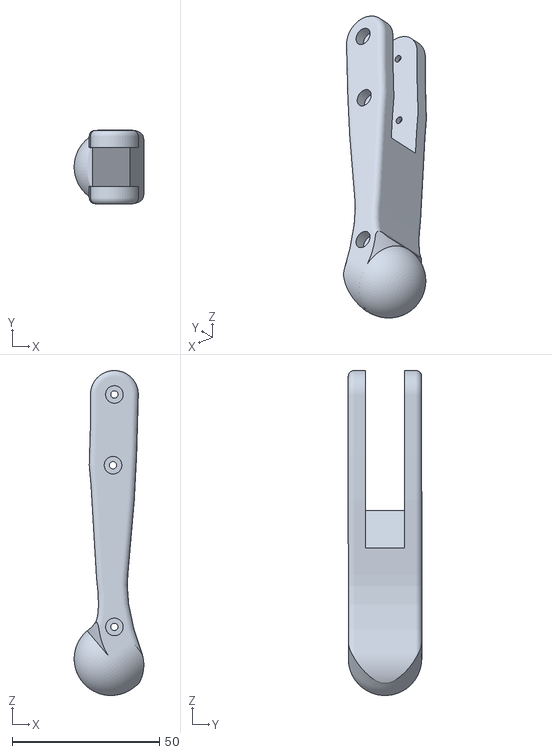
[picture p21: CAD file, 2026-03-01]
botzo_ros2_ws/urdf/meshes/BL_tibia.stl
23.7 x 25.0 x 110.5

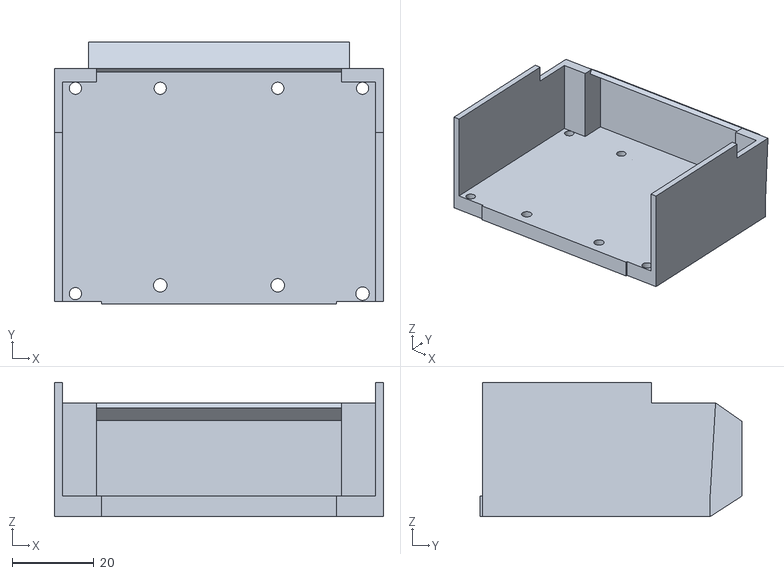
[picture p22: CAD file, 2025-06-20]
CAD_files/designs/body/plaque_right(printed).stl
80.6 x 64.1 x 32.9

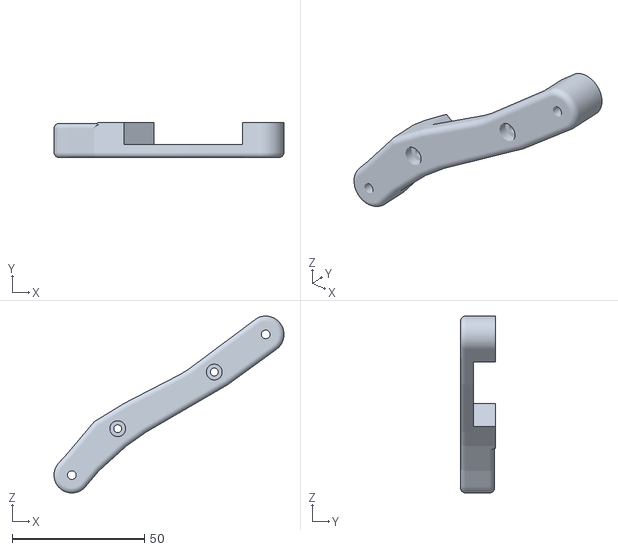
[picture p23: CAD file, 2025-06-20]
CAD_files/designs/legs/FL_knee_up_right.stl
87.0 x 13.3 x 66.9

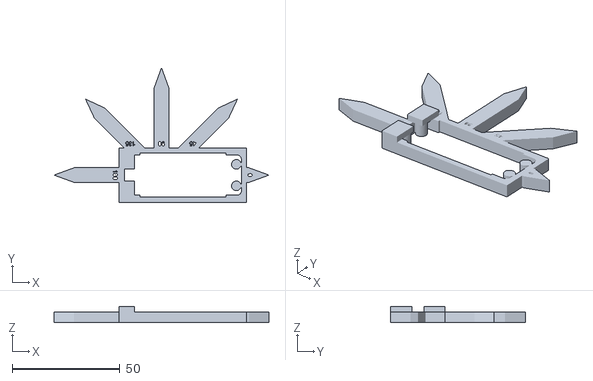
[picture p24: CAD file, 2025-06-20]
CAD_files/designs/servo_calibration_tools/tibia_calibration_tool.stl
100.0 x 62.7 x 7.50

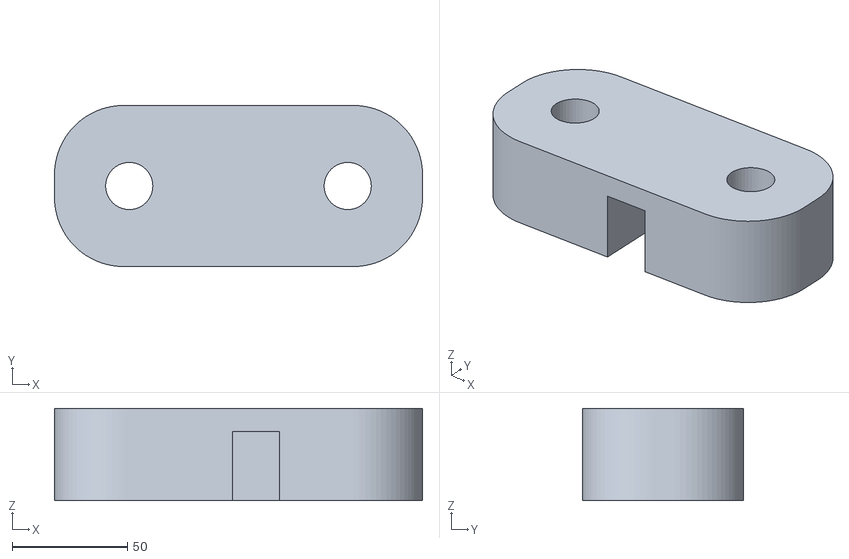
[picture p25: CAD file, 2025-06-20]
CAD_files/designs/testing_support/support_test_leg.stl
160.0 x 70.0 x 40.0

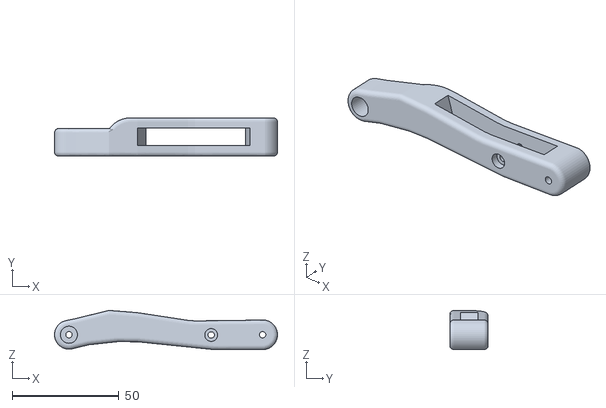
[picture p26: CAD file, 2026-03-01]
botzo_ros2_ws/urdf/meshes/BR_femur.stl
104.3 x 18.0 x 18.4

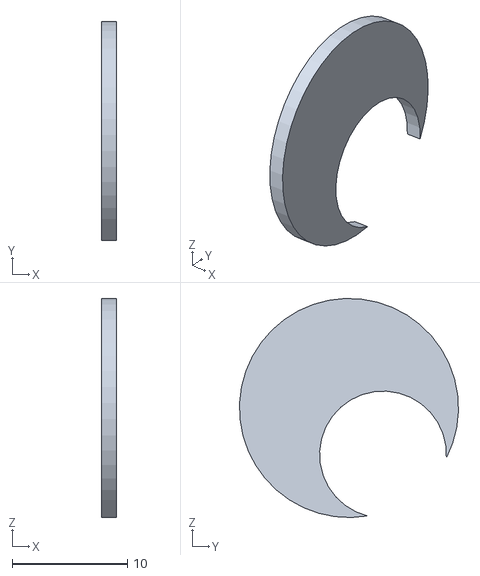
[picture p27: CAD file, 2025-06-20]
CAD_files/designs/body/right_eye.stl
1.30 x 19.0 x 19.0

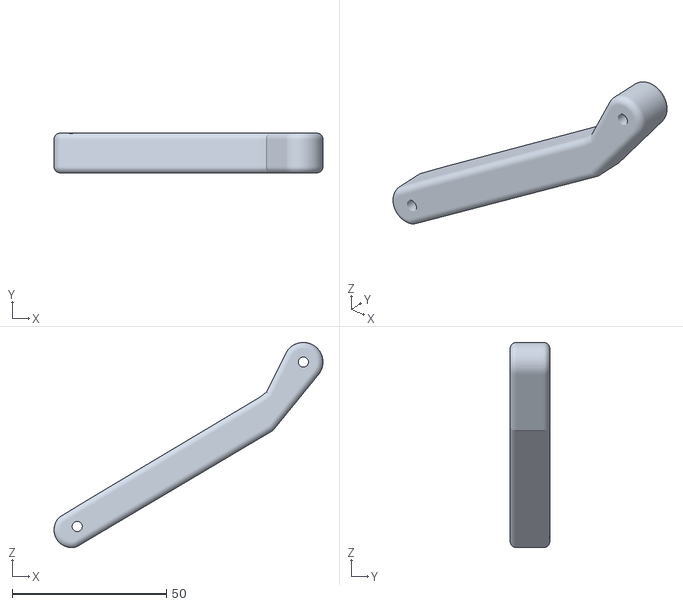
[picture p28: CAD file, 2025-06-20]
CAD_files/designs/legs/FL_knee_down.stl
87.2 x 12.9 x 66.5

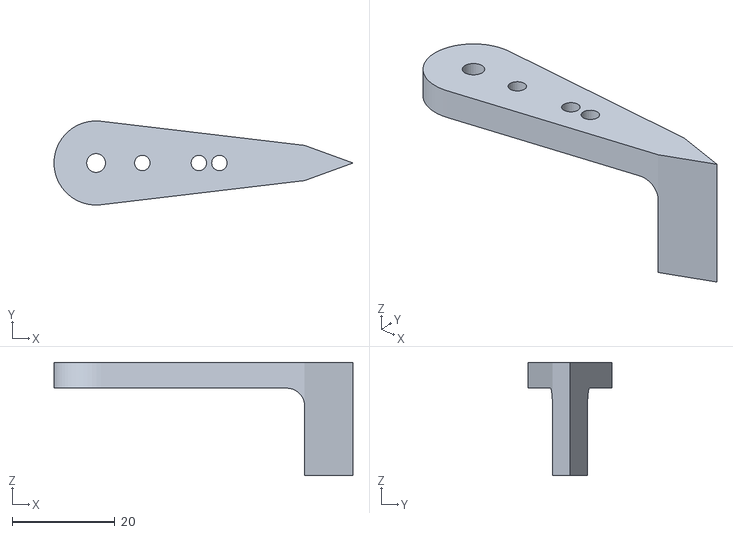
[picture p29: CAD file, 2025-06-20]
CAD_files/designs/servo_calibration_tools/arm_for_calibration_tool.stl
58.2 x 16.4 x 22.0

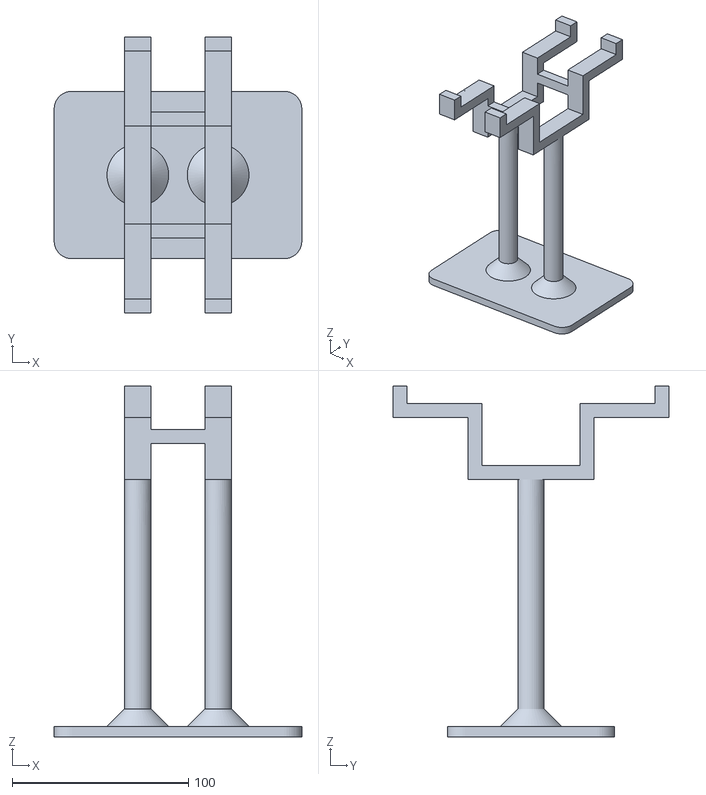
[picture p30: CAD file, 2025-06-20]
CAD_files/designs/testing_support/support_test_body.stl
140.6 x 156.9 x 199.2

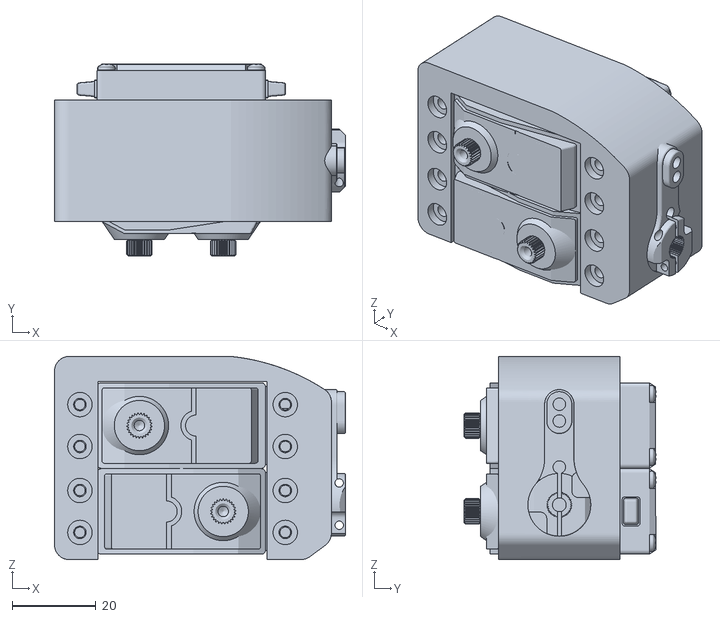
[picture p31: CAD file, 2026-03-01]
botzo_ros2_ws/urdf/meshes/BL_shoulder.stl
69.4 x 45.9 x 48.5

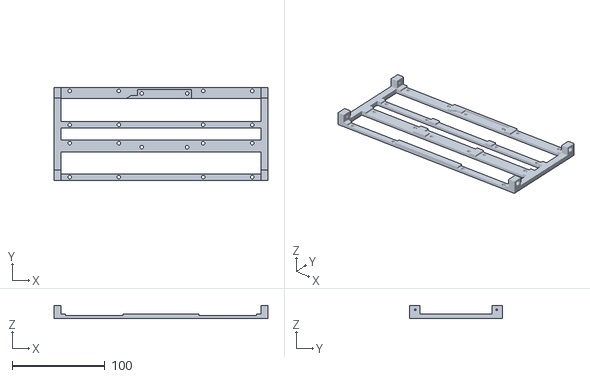
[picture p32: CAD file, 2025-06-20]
CAD_files/designs/body/internal_infrastructure(printed).stl
231.0 x 99.9 x 14.0

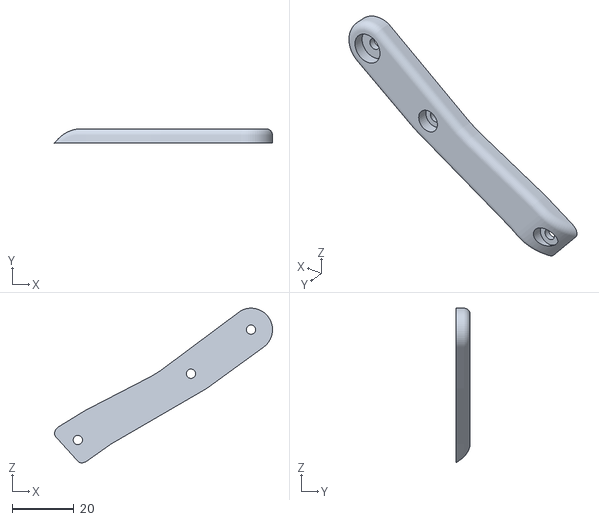
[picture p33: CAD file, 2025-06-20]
CAD_files/designs/legs/FL_knee_up_left.stl
70.4 x 4.65 x 50.0

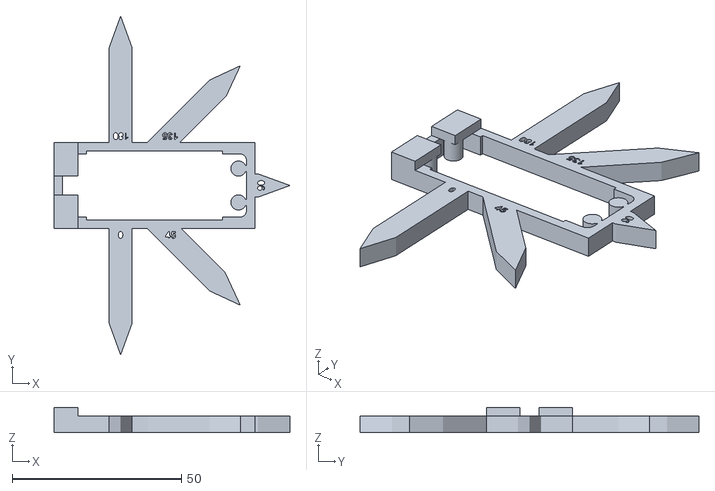
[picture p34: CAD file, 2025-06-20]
CAD_files/designs/servo_calibration_tools/shoulder_calibration_tool.stl
69.7 x 100.0 x 7.50

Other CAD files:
CAD_files/designs/testing_support/support_test_leg_base.stl
botzo_ros2_ws/urdf/meshes/FL_tibia.stl
CAD_files/designs/body/plaque_left(printed).stl
CAD_files/designs/legs/FR_foot.stl
CAD_files/designs/body/battery_box_holder(printed).stl
CAD_files/designs/body/bottom_base(printed).stl
CAD_files/designs/body/front_face(print).stl
CAD_files/designs/body/left_eye.stl
CAD_files/designs/body/lid_battery(printed).stl
CAD_files/designs/body/rear(printed).stl
CAD_files/designs/body/top(printed).stl
CAD_files/designs/legs/BL_ankle_left.stl
CAD_files/designs/legs/BL_ankle_right.stl
CAD_files/designs/legs/BL_connector.stl
CAD_files/designs/legs/BL_foot.stl
CAD_files/designs/legs/BL_holder.stl
CAD_files/designs/legs/BL_knee_down.stl
CAD_files/designs/legs/BL_knee_up_left.stl
CAD_files/designs/legs/BL_knee_up_right.stl
CAD_files/designs/legs/BR_ankle_left.stl
CAD_files/designs/legs/BR_ankle_right.stl
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

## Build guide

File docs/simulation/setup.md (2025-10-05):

# Botzo Simulation

leg

To create a digital twin of our real robot we built a URDF file from the CAD model in Fusion 360 (for more details see [here](https://ieroboticsailab.github.io/botzo/build/cad/urdf/)). A URDF file is a format used in robotics to describe the physical properties of a robot, including its geometry, links and meshes positions. It allows for simulation and visualization of the robot in simulation environments.

The goal will be to create an exact twin of botzo in a digital space, allowing us to test algorithms, simulate movements, and visualize the robot's behavior without needing the physical hardware. This is particularly useful for testing and development purposes.

Our final aim is to train and teach botzo to perform tasks using Reinforcement Learning in simulator engines such as Pybullet + Mujoco or IsaacLab. This will allow Botzo to learn how to stabilize his walking, climb stairs and even perform tricks like jumping or dancing, all in a safe and controlled environment before applying the learned behaviors to the physical robot. 

## `simulation/` folder

!!! note

    We recommend to create a virtual environment to run the code in this folder, and install PyBullet and Numpy.

- `utils/`: Contains a script used by the simulations scripts to import our Inverse Kinematics algorithm, which is used to calculate the angles of the motors based on the desired position of the robot's feet. Using the exact same algorithm used in the real robot, we can ensure that the simulation behaves similarly to the physical robot. (find [here](https://github.com/IERoboticsAILab/botzo/tree/main/simulation/utils))

- PyBullet scripts:
  - `spawn_botzo.py`: Load URDF, basic script of PyBullet (find [here](https://github.com/IERoboticsAILab/botzo/tree/main/simulation/spawn_botzo.py))
  - `move_one_joint.py`: Just to showcase how we access and move joints in Pybullet. So in this script we move one joint of botzo (find [here](https://github.com/IERoboticsAILab/botzo/tree/main/simulation/move_one_joint.py))
  - `debugger.py`: A script that allow us to move specific joints defined by the user. It is used to find the joint zeros, so we create a [function](https://github.com/IERoboticsAILab/botzo/blob/main/simulation/utils/IK_solver.py#L90) that transform simulation joint to real joint position (find [here](https://github.com/IERoboticsAILab/botzo/tree/main/simulation/debugger.py))
  - `IK_one_leg.py`: A script to test and visualize the Inverse Kinematics algorithm for one leg of botzo in PyBullet. It allows us to see how the IK algorithm calculates the joint angles needed to position the leg's foot at a desired location in 3D space. (find [here](https://github.com/IERoboticsAILab/botzo/tree/main/simulation/IK_one_leg.py))
  - `digital_twin.py`: The main script to simulate the full botzo robot in PyBullet using the URDF file. It incorporates the Inverse Kinematics algorithm to control the robot's movements, allowing us to test and visualize how botzo would behave in a digital environment. (find [here](https://github.com/IERoboticsAILab/botzo/blob/main/simulation/digital_twin.py))

---

[BOTZO SIMULATION REPO](https://github.com/IERoboticsAILab/botzo/tree/main/simulation)

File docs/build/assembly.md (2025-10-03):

!!! info

    To be done!

leg

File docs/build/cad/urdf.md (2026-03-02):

# Robot URDF

botzo

[OWR URDF](https://github.com/IERoboticsAILab/botzo/blob/main/CAD_files/URDF/BOTZO_URDF_description/urdf/BOTZO_URDF.urdf)

## What is a URDF and why we need it?

A URDF is a file used in robotics to import the robot in a simulation. It uses the STL/CAD files as a base. Assemble them with rigid or rotatory joins, and save positions of each bone and pivot in the joints. To sum up, it is file that describe your robot in deep details and precision.

## How to create a URDF for Botzo

From the CAD files, we created a URDF file for Botzo using Fusion 360 and [fusion2urdf](https://github.com/syuntoku14/fusion2urdf). A repo that give us a package for exporting URDF from a Fusion 360 packages.

Visit directly the repos if you don't understand something. This is a resume of what they do:

- [Webgraphviz](http://www.webgraphviz.com/) (for debugging purposes)

- [fusion2urdf](https://github.com/syuntoku14/fusion2urdf) (for exporting URDF from Fusion 360 file assembled with joints)

## Result and prcedure

You will use [BOTZO_F360_JOINS.f3d](https://github.com/IERoboticsAILab/botzo/blob/main/CAD_files/URDF/BOTZO_F360_JOINS.f3d) file to build your urdf, or just use ours [here](https://github.com/IERoboticsAILab/botzo/blob/main/CAD_files/URDF/BOTZO_URDF_description/urdf/BOTZO_URDF.urdf).

## Botzo description

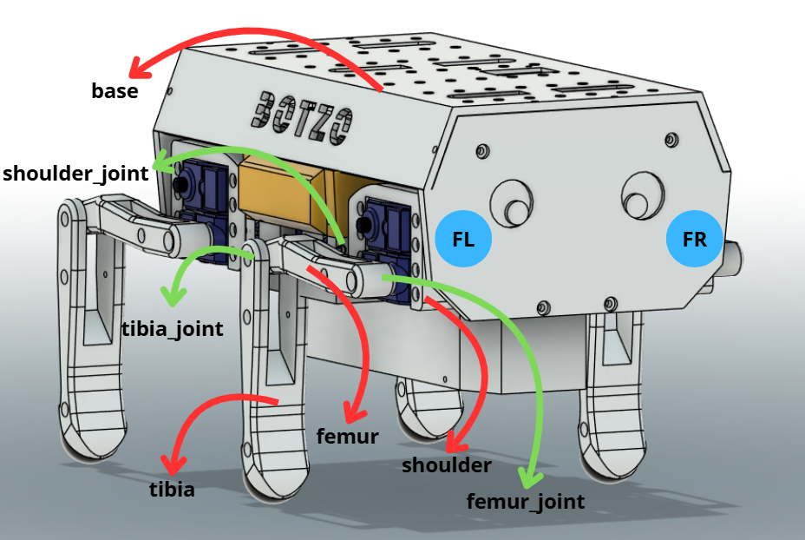
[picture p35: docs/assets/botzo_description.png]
botzo_description


### Prepare STL
As stated in the [Fusion2PyBullet repo](https://github.com/yanshil/Fusion2PyBullet) and [fusion2urdf](https://github.com/syuntoku14/fusion2urdf), we must **prepare our STL** file properly with strict rules:

1. All bodies/peaces/future links must be **components**.
2. Add physical materials
3. Add **joint** to connect all components. In fusion you can select various type of joint (static, rotational, etc...) and also the pivot point.
4. Call one component as `base_link`
5. Remove links of components (if the are right click on it and press Break Link)
6. Check STL joint-link structure using [Webgraphviz](http://www.webgraphviz.com/). Here how:
    - Download [Joint2Graphviz repo](https://github.com/yanshil/Joint2Graphviz) as a ZIP.
    - Extract the ZIP in a known directory.
    - Open terminal:

        ```powershell
        cd <path to Joint2Graphviz>

        Copy-Item ".\Joint2Graphviz-master\" -Destination "${env:APPDATA\Autodesk\Autodesk Fusion 360\API\Scripts\" -Recurse
        ```

        For me was:
        ```powershell
         cd C:\Users\orlan\OneDrive\Desktop\side_projects\Joint2Graphviz-master

         Copy-Item "..\Joint2Graphviz-master\" -Destination "..\..\..\..\AppData\Roaming\Autodesk\Autodesk Fusion 360\API\Scripts\" -Recurse
        ```
    - Now the script to create a `.txt` file for your link graph is added to fusion
    - Open fusion
    - Open the file of the robot
    - Go to utility > Addins
    - Under `My Script` you should see `Joint2Graphviz`
    - Press it. It will create a `graph.txt`

    - Copy and pase the text content to [Webgraphviz](http://www.webgraphviz.com/) and check your robot tf structure to be valid.

**(for more infors check [Joint2Graphviz readme](https://github.com/yanshil/Joint2Graphviz))**

-----

!!! warning
    
    7. We discovered that URDF does NOT suport close loop. Our leg design is one big close loop. You can check `wrong_graph` folder to see a graph with a close loop... The URDF won't work if there is a close loop

## Export URDF

1. Download [fusion2urdf](https://github.com/syuntoku14/fusion2urdf)
2. Extract the ZIP in a known directory.
3. Open terminal:

    ```powershell
    cd <path to Fusion2PyBullet>

    Copy-Item ".\URDF_Exporter\" -Destination "${env:APPDATA}\Autodesk\Autodesk Fusion 360\API\Scripts\" -Recurse
    ```

    For me was:
    ```powershell
        PS C:\Users\orlan\OneDrive\Desktop\side_projects\Fusion2PyBullet-master> Copy-Item ".\Bullet_URDF_Exporter\" -Destination "..\..\..\..\AppData\Roaming\Autodesk\Autodesk Fusion 360\API\Scripts\" -Recurse
    ```
4. Open fusion > utils > addins > my scripts > Bullet_URDF_Exporter

**(for more infors check [fusion2urdf readme](https://github.com/syuntoku14/fusion2urdf/blob/master/README.md) or [Fusion2PyBullet readme](https://github.com/yanshil/Fusion2PyBullet/blob/master/README.md))**

5. You will recive a folder with all the scrips and files to simulate your robot in ROS/Gazebo or PyBullet. To simply extract the URDF from XACRO use this comand:
    
    ```bash
    ros2 run xacro xacro <your_file>.xacro > <your_file>.urdf
    ```

6. [OWR URDF](https://github.com/IERoboticsAILab/botzo/blob/main/CAD_files/URDF/BOTZO_URDF_description/urdf/BOTZO_URDF.urdf)

---

[BOTZO URDF REPO](https://github.com/IERoboticsAILab/botzo/tree/main/CAD_files/URDF)

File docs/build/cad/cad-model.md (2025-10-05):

# CAD Model

Botzo CAD Model

Botzo has been primarily designed using Fusion 360 CAD software. To support this,
we provide a `.f3z` file that can be imported directly into Fusion 360. Additionally,
`.step` files are available for users who prefer other CAD software.

Since Botzo is designed for 3D printing, all printable components are provided as
STL files. These are ready to be loaded into a slicer and printed using an FDM
printer.

All CAD files are available in the Botzo repository: [📁 View on GitHub](https://github.com/IERoboticsAILab/botzo/tree/main/CAD_files/designs)

## About the Design

### The Leg

The leg design was inspired by the project [Chop](https://hackaday.io/project/171456-diy-hobby-servos-quadruped-robot/details)
by _Miguel Ayusto Parrilla_. By concentrating most of the weight in the shoulder,
this design reduces leg inertia, improving walking stability.

Leg

### The Body

The body is designed to house all internal components and cable routing while
leaving space on the dorsal side for mounting additional modules like a LiDAR or
webcams—supporting future capabilities like mapping and vision.

Body

---

[BOTZO CAD REPO](https://github.com/IERoboticsAILab/botzo/tree/main/CAD_files)

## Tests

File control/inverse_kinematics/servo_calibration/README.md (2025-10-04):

<div align="center">
<h1>BOTZO 🐾</h1>

**`The good boy quadruped robot :)`**

<p align="center">
    <a href="https://www.instagram.com/botzo.ie/" target="_blank" rel="noopener noreferrer">
        
    </a>
    <a href="" target="_blank" rel="noopener noreferrer">
        
    </a>
    <a href="mailto:botzoteam@gmail.com">
        
    </a>
    <a href="">
        
    </a>

more about botzo [here](https://github.com/IERoboticsAILab/botzo)

for specific Servo Calibration documentation [here](https://ieroboticsailab.github.io/botzo/learn/servo-calibration/)

| Before Calibration | After Calibration |
| --- | --- |
| Before Calibration | After Calibration |

</p>
</div>

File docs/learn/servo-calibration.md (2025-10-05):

# Servo Calibration

!!! note

    This guide can be quite improved.

Servos work by using PWM (Pulse Width Modulation) signals, where different pulse  
widths correspond to specific angles. Typically, this ranges between 500 µs and  
2000 µs. However, due to manufacturing tolerances—especially in more affordable  
servos—there can be significant variation in how each servo responds to the same  
PWM signal.

To improve accuracy, each servo can be calibrated to determine its specific PWM  
response curve. This only requires some simple math and a bit of setup.

## Result

| Before Calibration | After Calibration |
| --- | --- |
| Before Calibration | After Calibration |

With calibration, servo motion becomes noticeably more accurate and consistent.

## Repo Content

1. `Calibration_Procedure.ipynb`: A Google Colab notebook that fits a least-squares  
   regression to convert angles to PWM values specific to each servo.

2. `calibarte_servos.ino`: Arduino code to help identify real PWM values using the  
   [Calibration Tool](https://github.com/IERoboticsAILab/botzo/tree/main/CAD_files/designs/servo_calibration_tools).

3. `save_coefficients/`: Folder containing `.csv` and `.xlsx` files used to store  
   calibration data for each leg and servo.

## Background and Motivation

Servos are controlled by PWM signals to reach a given angle. However, each servo  
has unique mechanical and electrical characteristics that lead to deviations between  
the **desired** angle and the **actual** angle achieved.

This calibration process helps:

1. Measure how each servo responds to standard angles.
2. Fit a custom curve (linear or quadratic) for more accurate angle-to-PWM mapping.

The theoretical formula from datasheets is often:

- **PWM = 7.4 × desired_angle + 500**

So for example:

- `[0, 45, 90, 135, 180]` degrees → `[500, 833, 1166, 1500, 1832]` PWM values

However, these are idealized values—calibration helps find the real-world equivalent.

## Process of Calibration

1. **Compute ideal PWM values**  
   Use Cell 1 of the notebook to calculate PWM values for known angles using the  
   datasheet formula.

2. **Align servo using Arduino code**  
   Upload the [Arduino sketch](https://github.com/IERoboticsAILab/botzo/blob/main/control/inverse_kinematics/servo_calibration/calibarte_servos.ino)  
   and use the serial monitor to manually tune PWM values until the servo aligns with  
   target angles (0°, 45°, 90°, 135°, 180°).

3. **Record the actual PWM values**  
   Example values from the Front Right leg:

   ```python
   real_pwm_SFR = np.array([564, 890, 1219, 1564, 1897])
   real_pwm_FFR = np.array([606, 930, 1265, 1606, 1930])
   real_pwm_TFR = np.array([555, 895, 1230, 1580, 1910])
   ```

4. **Fit a regression curve**  
   Use least-squares regression to generate coefficients for the curve that maps  
   desired degrees to PWM for each servo.

5. **Test and verify accuracy**  
   Use the new function to convert angles into PWM and verify improved motion accuracy.

---

## Cell 1 – Setup and PWM Conversion

```python
# Libraries
import numpy as np

# Convert desired angles (degrees) to PWM using datasheet formula
def deg2PWM(desire_deg_angles):
    output = []
    for angle in desire_deg_angles:
        pulse = round((7.4074 * angle) + 500, 0)
        output.append(pulse)
        print(f"// {angle} degrees => {pulse} PWM")
    return output

# Example usage
desire_angles = [0, 45, 90, 135, 180, 270]
desired_PWM = deg2PWM(desire_angles)
print("\nDesired PWM values:", desired_PWM)

print("\nPlease run these PWM signals and record the actual angles reached.")
```

---

## Arduino Procedure

1. Upload the Arduino sketch.
2. Open the serial monitor and set the PWM to 500.
3. Attach the servo arm using the [calibration tools](https://github.com/IERoboticsAILab/botzo/tree/main/CAD_files/designs/servo_calibration_tools) aligned as closely as possible to 0°.
4. Adjust the PWM value until the arm aligns perfectly with 0°.
5. Record the PWM, and repeat for 45°, 90°, 135°, and 180°.

---

## Cell 2 – Save Real PWM Values

```python
real_pwm_SFR = np.array([564, 890, 1219, 1564, 1897])
```

---

## Cell 3 – Run Regression

```python
import matplotlib.pyplot as plt

# Input: degrees and corresponding real PWM values
degrees = np.array([0, 45, 90, 135, 180])
real_pwm = real_pwm_SFR  # Replace with your servo data

# Fit a quadratic regression curve
coefficients = np.polyfit(degrees, real_pwm, 2)
a, b, c = coefficients

print(f"Quadratic coefficients: a = {a}, b = {b}, c = {c}")

# Plotting
plt.scatter(degrees, real_pwm, color='blue', label='Measured data')
x_vals = np.linspace(0, 180, 1000)
y_vals = a * x_vals**2 + b * x_vals + c
plt.plot(x_vals, y_vals, color='red', label=f'Fit: {a:.2f}x² + {b:.2f}x + {c:.2f}')
plt.xlabel('Degrees')
plt.ylabel('PWM')
plt.title('Servo Calibration Curve')
plt.legend()
plt.grid(True)
plt.show()
```

---

## Notes

- Calibrate **each servo** individually, as they may have different characteristics.
- Keep the servo horn attached after calibration—removing it will require redoing the process.
- Store your coefficients securely for consistent motion across reboots or deployments.

By following this process, you’ll significantly improve servo positioning accuracy,  
making your robot’s motion more reliable and repeatable.

---

[BOTZO SERVO CALIBRATION REPO](https://github.com/IERoboticsAILab/botzo/tree/main/control/inverse_kinematics/servo_calibration)

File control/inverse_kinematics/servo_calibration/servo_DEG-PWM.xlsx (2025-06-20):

DATASHEET
DESIRE | PWM
0 | 500
135 | 1500
270 | 2500
DIFF | DIFF | SLOPE
135 | 1000 | 7.407407407
 |  |  |  |  | PWM(X) = ax^2 + bx + c
 |  |  |  |  | least squares regression to find the coefficients a, b, and c by solving the system of equations.
FRONT RIGHT |  |  |  |  | COEFFICIENTS
SERVO NAME | DESIRE DEGREE | EXPECTED PWM | REAL PWM | DIFF | a | b | c
SFR | 0 | 500 | 600 | 100 | 0 | 7.378 | 616
 | 45 | 833 | 933 | 100
 | 90 | 1167 | 1267 | 100
 | 135 | 1500 | 1620 | 120
 | 180 | 1833 | 1940 | 107
FFR | 0 | 500 | 580 | 80 | 0 | 7.682 | 578.142
 | 45 | 833 | 920 | 87
 | 90 | 1167 | 1260 | 93
 | 135 | 1500 | 1610 | 110
 | 180 | 1833 | 1935 | 102
TFR | 0 | 500 | 620 | 120 | 0 | 7.314 | 619.028
 | 45 | 833 | 950 | 117
 | 90 | 1167 | 1278 | 111
 | 135 | 1500 | 1630 | 130
 | 180 | 1833 | 1960 | 127
FRONT LEFT |  |  |  |  | COEFFICIENTS
SERVO NAME | DESIRE DEGREE | EXPECTED PWM | REAL PWM | DIFF | a | b | c
SFL | 0 | 500 | 640 | 140 | 0 | 7.649 | 638.486
 | 45 | 833 | 980 | 147
 | 90 | 1167 | 1320 | 153
 | 135 | 1500 | 1670 | 170
 | 180 | 1833 | 1999 | 166
FFL | 0 | 500 | 630 | 130 | 0 | 7.603 | 625.428
 | 45 | 833 | 960 | 127
 | 90 | 1167 | 1310 | 143
 | 135 | 1500 | 1670 | 170
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

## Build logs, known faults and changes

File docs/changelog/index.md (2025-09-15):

# Changelog

!!! tip

    This can serve a place where we can write for example every month what has been
    accomplished, or if some important step has been made. As a possible way of doing this can be
    the following. Furthermore, we can use automated tools like [git-cliff](https://git-cliff.org/) to generate
    good looking changelogs based on the commit messages.

## 06/08/2025 - Initial Draft

This marks the beginning of having a proper documentation for our project Botzo.
We have added support to generate documentation using [material mkdocs](https://squidfunk.github.io/mkdocs-material/)...

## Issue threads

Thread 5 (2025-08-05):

CAD files format

PedroS235, 2025-08-05:
Currently, only STL or Fusion360 files are available for the different CAD parts. However, not everyone uses Fusion360, but Solidworks or OnShape for example.

It would be great if you could also provide .stp/.step files, maybe of the entire assembly too.

GRINGOLOCO7, 2025-08-06:
https://github.com/IERoboticsAILab/botzo/blob/main/CAD_files/body/final_body.step

Thank you for the advice! Done, check [here](https://github.com/IERoboticsAILab/botzo/blob/main/CAD_files/body/final_body.step)

Closed 2025-08-06.

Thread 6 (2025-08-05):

Improving Project Structure

PedroS235, 2025-08-05:
When looking at first glance the project structure is a bit all over the place. In my opinion, you can structure the project in a more meaningful way. A possible structure could be something like:

```
.
|-- CAD (Include all the CAD files here
|-- firmware (This is where you can include the firmware running on the Arduino board for instance)
|-- simulation (Everything related to simulation)
|-- control (this is where you can have your algorithms. This could also be like ros_ws if you plan on usin ROS)
|-- docs (any piece of documentation)
|-- notebooks (all you jupyter notebooks)
|-- scripts
|--README.md
|-- ...
```

This is just an idea, of course it can be better ;)

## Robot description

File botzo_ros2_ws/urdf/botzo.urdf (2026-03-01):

<?xml version="1.0" ?>
<robot name="botzo">




  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


  

  <link name="base">
    <inertial>
      <origin rpy="0 0 0" xyz="0.0004582873296189677 -0.0002865140714721542 0.064627583528461"/>
      <mass value="0.7893620452930467"/>
      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
    </inertial>
    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
  </link>
  <link name="BL_shoulder">
    <inertial>
      <origin rpy="0 0 0" xyz="-0.03752793520024612 0.002007582464765928 0.010711593323082934"/>
      <mass value="0.10894741172095637"/>
      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
    </inertial>
    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
  </link>
  <link name="BR_shoulder">
    <inertial>
      <origin rpy="0 0 0" xyz="-0.03752795235962702 -0.0020133047527714915 0.010710440129393366"/>
      <mass value="0.10894732734955483"/>
      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
    </inertial>
    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
  </link>
  <link name="FL_shoulder">
    <inertial>
      <origin rpy="0 0 0" xyz="0.03733001797786554 0.0020131800950347473 0.010709605239346186"/>
      <mass value="0.10895629411716044"/>
      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
    </inertial>
    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
  </link>
  <link name="FR_shoulder">
    <inertial>
      <origin rpy="0 0 0" xyz="0.03733001634412595 -0.00201054852272476 0.010710033996158143"/>
      <mass value="0.1089563019083912"/>
      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
    </inertial>
    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
  </link>
  <link name="FR_femur">
    <inertial>
      <origin rpy="0 0 0" xyz="-0.04670121848460076 0.008185053377990609 0.0015481236726892916"/>
      <mass value="0.01663804705601809"/>
      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
    </inertial>
    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
  </link>
  <link name="FR_tibia">
    <inertial>
      <origin rpy="0 0 0" xyz="-0.00046565926526049445 -0.006596009939999856 -0.05485786854630329"/>
      <mass value="0.02685067474548009"/>
      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
    </inertial>
    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
  </link>
  <link name="FL_femur">
    <inertial>
      <origin rpy="0 0 0" xyz="-0.04670134392194205 -0.008187000609746323 0.0015498678648720662"/>
      <mass value="0.01663808878200678"/>
      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
    </inertial>
    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
  </link>
  <link name="FL_tibia">
    <inertial>
      <origin rpy="0 0 0" xyz="-0.00046566122225385874 0.006584330690178511 -0.054859540417466914"/>
      <mass value="0.026850714584678873"/>
      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
    </inertial>
    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
  </link>
  <link name="BR_femur">
    <inertial>
      <origin rpy="0 0 0" xyz="-0.04670048111666723 0.008184055329044218 0.001550627307348583"/>
      <mass value="0.0166380470560182"/>
      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
    </inertial>
    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
  </link>
  <link name="BR_tibia">
    <inertial>
      <origin rpy="0 0 0" xyz="-0.00046564986947178477 -0.006583418684337247 -0.05485980183517331"/>
      <mass value="0.0268506747454801"/>
      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
    </inertial>
    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
  </link>
  <link name="BL_femur">
    <inertial>
      <origin rpy="0 0 0" xyz="-0.04670076868330274 -0.008187978467027804 0.0015453975945706813"/>
      <mass value="0.016638088782005175"/>
      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
    </inertial>
    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
  </link>
  <link name="BL_tibia">
    <inertial>
      <origin rpy="0 0 0" xyz="-0.00046565182648261594 0.006613758250461149 -0.05485613170141751"/>
      <mass value="0.026850714584678158"/>
      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
    </inertial>
    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
  </link>




  <joint name="Revolute 1" type="continuous">
    <origin rpy="0 0 0" xyz="-0.04255 -0.0531 0.0522"/>
    <parent link="base"/>
    <child link="BL_shoulder"/>
    <axis xyz="-1.0 -0.0 -0.0"/>
  </joint>
  <joint name="Revolute 2" type="continuous">
    <origin rpy="0 0 0" xyz="-0.04255 0.0531 0.0522"/>
    <parent link="base"/>
    <child link="BR_shoulder"/>
    <axis xyz="1.0 0.0 0.0"/>
  </joint>
  <joint name="Revolute 3" type="continuous">
    <origin rpy="0 0 0" xyz="0.04255 -0.0531 0.0522"/>
    <parent link="base"/>
    <child link="FL_shoulder"/>
    <axis xyz="-1.0 -0.0 0.0"/>
  </joint>
  <joint name="Revolute 4" type="continuous">
    <origin rpy="0 0 0" xyz="0.04255 0.0531 0.0522"/>
    <parent link="base"/>
    <child link="FR_shoulder"/>
    <axis xyz="1.0 -0.0 -0.0"/>
  </joint>
  <joint name="Revolute 5" type="continuous">
    <origin rpy="0 0 0" xyz="0.048573 0.0188 -0.001579"/>
    <parent link="FR_shoulder"/>
    <child link="FR_femur"/>
    <axis xyz="0.0 1.0 0.0"/>
  </joint>
  <joint name="Revolute 6" type="continuous">
    <origin rpy="0 0 0" xyz="-0.090579 0.013 0.0"/>
    <parent link="FR_femur"/>
    <child link="FR_tibia"/>
    <axis xyz="0.0 1.0 0.0"/>
  </joint>
  <joint name="Revolute 7" type="continuous">
    <origin rpy="0 0 0" xyz="0.048573 -0.0188 -0.001575"/>
    <parent link="FL_shoulder"/>
    <child link="FL_femur"/>
    <axis xyz="-0.0 1.0 -0.000213"/>
  </joint>
  <joint name="Revolute 8" type="continuous">
    <origin rpy="0 0 0" xyz="-0.090579 -0.013 3e-06"/>
    <parent link="FL_femur"/>
    <child link="FL_tibia"/>
    <axis xyz="-0.0 1.0 -0.000213"/>
  </joint>
  <joint name="Revolute 9" type="continuous">
    <origin rpy="0 0 0" xyz="-0.029173 0.018801 -0.001575"/>
    <parent link="BR_shoulder"/>
    <child link="BR_femur"/>
    <axis xyz="-0.0 1.0 0.000241"/>
  </joint>
  <joint name="Revolute 10" type="continuous">
    <origin rpy="0 0 0" xyz="-0.090579 0.013 4e-06"/>
    <parent link="BR_femur"/>
    <child link="BR_tibia"/>
    <axis xyz="-0.0 1.0 0.000241"/>
  </joint>
  <joint name="Revolute 11" type="continuous">
    <origin rpy="0 0 0" xyz="-0.029173 -0.018799 -0.001585"/>
    <parent link="BL_shoulder"/>
    <child link="BL_femur"/>
    <axis xyz="-0.0 1.0 0.000326"/>
  </joint>
  <joint name="Revolute 12" type="continuous">
    <origin rpy="0 0 0" xyz="-0.090579 -0.013 -4e-06"/>
    <parent link="BL_femur"/>
    <child link="BL_tibia"/>
    <axis xyz="-0.0 1.0 0.000326"/>
  </joint>
</robot>

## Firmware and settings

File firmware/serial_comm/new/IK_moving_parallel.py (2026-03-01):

import numpy as np
import serial
import time
import threading
import os
import sys
import controller_dict_parallel as controller_dict
import hardcoded_skills_parallel as skills
from imu_stabilizer import IMUStabilizer

# Add the current directory to the system path to ensure imports work correctly
current_dir = os.path.dirname(os.path.abspath(__file__))
if current_dir not in sys.path:
    sys.path.insert(0, current_dir)

# Import IK functions
from IK_Funcs import *

# Global variables
ser = None  # Serial connection to Arduino
current_position = [0, 3, 15]  # Start at home position

# Serial communication settings
SERIAL_BAUD_RATE = 500000 
STEP_DELAY = 0.05  # Delay between steps for reliable communication
SERIAL_TIMEOUT = 1.0  # Timeout for serial communication

# Joystick settings
JOYSTICK_THRESHOLD = 0.3  # Threshold for joystick activation

# Serial port options to try (in order of preference)
SERIAL_PORTS = ['/dev/ttyACM0', '/dev/ttyACM1', '/dev/ttyUSB0', '/dev/ttyUSB1']

# IMU stabilization settings
IMU_UPDATE_HZ = 100.0
# Gain from tilt angle (deg) to leg Z correction (cm). Tune carefully.
# If the robot leans in the direction of correction, invert the sign.
ROLL_GAIN_Z_PER_DEG = -0.08  # cm per degree (negative to invert previous behavior)
PITCH_GAIN_Z_PER_DEG = 0.08
MAX_Z_CORRECTION_CM = 1.5
# Ignore tiny tilts to avoid oscillation
ROLL_PITCH_DEADBAND_DEG = 2.0
# Smoothing and slew rate limiting to avoid sudden asymmetric corrections
CORR_SMOOTH_ALPHA = 0.18  # stronger smoothing
MAX_DELTA_Z_PER_STEP_CM = 0.12
STANCE_Z_THRESHOLD = 15.5  # apply correction only when target z >= threshold (stance phase)
RATE_DAMPING_GAIN_CM_PER_DPS = 0.01  # additional damping proportional to rate

# Keep previous per-leg Z corrections for smoothing/slew
prev_leg_z_corrections = [0.0, 0.0, 0.0, 0.0]

def _apply_imu_stabilization(coordinates):
    """Apply small Z offsets to each leg based on current roll/pitch from IMU.
    coordinates: [[x,y,z], ...] for FR, FL, BR, BL
    Returns adjusted coordinates list.
    """
    global imu
    if imu is None:
        return coordinates
    try:
        ori = imu.get_orientation()
        roll = ori.get('roll', 0.0)
        pitch = ori.get('pitch', 0.0)
        rates = imu.get_rates()
        roll_rate = rates.get('roll_rate', 0.0)
        pitch_rate = rates.get('pitch_rate', 0.0)

        # Deadband to avoid constant micro-corrections
        if abs(roll) < ROLL_PITCH_DEADBAND_DEG:
            roll = 0.0
        if abs(pitch) < ROLL_PITCH_DEADBAND_DEG:
            pitch = 0.0

        # Compute Z corrections per leg to counteract tilt.
        # Map angles to Z corrections. Sign of gains determines direction.
        roll_corr = ROLL_GAIN_Z_PER_DEG * roll
        pitch_corr = PITCH_GAIN_Z_PER_DEG * pitch

        # Leg order: FR, FL, BR, BL
        # Add viscous damping based on angular rates to fight oscillation
        roll_damp = RATE_DAMPING_GAIN_CM_PER_DPS * roll_rate
        pitch_damp = RATE_DAMPING_GAIN_CM_PER_DPS * pitch_rate

        raw_corrections = [
            -roll_corr - pitch_corr - roll_damp - pitch_damp,  # FR
            +roll_corr - pitch_corr + roll_damp - pitch_damp,  # FL
            -roll_corr + pitch_corr - roll_damp + pitch_damp,  # BR
            +roll_corr + pitch_corr + roll_damp + pitch_damp   # BL
        ]

        # Apply only on stance legs to avoid disturbing swing trajectory
        # Also smooth and slew-limit per leg
        global prev_leg_z_corrections
        smoothed = prev_leg_z_corrections[:]
        applied_mask = [False, False, False, False]
        for leg_idx, target in enumerate(coordinates):
            x, y, z = target
            if z >= STANCE_Z_THRESHOLD:
                applied_mask[leg_idx] = True
                desired = max(-MAX_Z_CORRECTION_CM, min(MAX_Z_CORRECTION_CM, raw_corrections[leg_idx]))
                # Low-pass filter
                filtered = smoothed[leg_idx] + CORR_SMOOTH_ALPHA * (desired - smoothed[leg_idx])
                # Slew-rate limit
                delta = filtered - smoothed[leg_idx]
                if delta > MAX_DELTA_Z_PER_STEP_CM:
                    delta = MAX_DELTA_Z_PER_STEP_CM
                elif delta < -MAX_DELTA_Z_PER_STEP_CM:
                    delta = -MAX_DELTA_Z_PER_STEP_CM
                smoothed[leg_idx] = smoothed[leg_idx] + delta
            else:
                # During swing, don't apply correction
                smoothed[leg_idx] = 0.0

        # Enforce diagonal symmetry only when both legs of the diagonal are in stance
        # Diagonal pairs: (FR, BL) -> (0,3), (FL, BR) -> (1,2)
        for a, b in [(0, 3), (1, 2)]:
            if applied_mask[a] and applied_mask[b]:
                mean_val = 0.5 * (smoothed[a] + smoothed[b])
                smoothed[a] = mean_val
                smoothed[b] = mean_val

        # Soft zero-sum: remove only a fraction of the mean to avoid large swings
        applied_values = [smoothed[i] for i in range(4) if applied_mask[i]]
        mean_corr = sum(applied_values) / len(applied_values) if applied_values else 0.0
        mean_remove_factor = 0.7
        for i in range(4):
            if applied_mask[i]:
                smoothed[i] -= mean_remove_factor * mean_corr

        # Update state
        prev_leg_z_corrections = smoothed

        # Apply corrections
        adjusted = []
        for leg_idx, target in enumerate(coordinates):
            x, y, z = target
            if applied_mask[leg_idx]:
                z_adj = z + smoothed[leg_idx]
            else:
                z_adj = z  # never alter swing legs
            adjusted.append([x, y, z_adj])
        return adjusted
    except Exception as e:
        print(f"IMU stabilization error: {e}")
        return coordinates

def move_legs_to_pos(coordinates):
    """Move legs to the specified coordinates"""
    global ser
    
    if ser is None or not ser.is_open:
        print("ERROR: Serial connection is not open. Cannot send movement commands.")
        return
    
    # Unpack coordinates for each leg
    FR_target, FL_target, BR_target, BL_target = coordinates

    # Apply IMU-based stabilization
    coordinates = _apply_imu_stabilization([FR_target, FL_target, BR_target, BL_target])
    FR_target, FL_target, BR_target, BL_target = coordinates
    
    # Calculate IK for each leg
    try:
        # Calculate angles and pulses for each leg
        FR_leg_angles = [FR_legIK(FR_target[0], FR_target[1], FR_target[2])]
        FR_leg_pulses = deg2PWM_set_angles(FR_leg_angles, coefficents_SFR, coefficents_FFR, coefficents_TFR)
        
        FL_leg_angles = [FL_legIK(FL_target[0], FL_target[1], FL_target[2])]
        FL_leg_pulses = deg2PWM_set_angles(FL_leg_angles, coefficents_SFL, coefficents_FFL, coefficents_TFL)
        
        BL_leg_angles = [BL_legIK(BL_target[0], BL_target[1], BL_target[2])]
        BL_leg_pulses = deg2PWM_set_angles(BL_leg_angles, coefficents_SBL, coefficents_FBL, coefficents_TBL)
        
        BR_leg_angles = [BR_legIK(BR_target[0], BR_target[1], BR_target[2])]
        BR_leg_pulses = deg2PWM_set_angles(BR_leg_angles, coefficents_SBR, coefficents_FBR, coefficents_TBR)
        
        # Format the serial message
        fr = FR_leg_pulses[0]
        fl = FL_leg_pulses[0]
        br = BR_leg_pulses[0]
        bl = BL_leg_pulses[0]
        msg = f"{fr[0]},{fr[1]},{fr[2]},{fl[0]},{fl[1]},{fl[2]},{br[0]},{br[1]},{br[2]},{bl[0]},{bl[1]},{bl[2]}\n"
        
        # Send directly to Arduino
        ser.reset_input_buffer()
        ser.write(msg.encode('utf-8'))
        ser.flush()
        
    except Exception as e:
        print(f"Error calculating or sending pulse values: {e}")

def process_controller_inputs():
    """
    Process controller inputs and map them to robot actions
    """
    # Get current joystick values
    left_y = -controller_dict.get_axis_value("LEFT_STICK_Y")  # Invert Y axis so positive is forward
    right_x = controller_dict.get_axis_value("RIGHT_STICK_X")  # Positive is right
    
    # Check for one-time button presses
    if controller_dict.button_just_pressed("TRIANGLE"):
        print("Triangle pressed - Going to home position")
        skills.skill_executor.go_home()
    
    if controller_dict.button_just_pressed("SQUARE"):
        print("Square pressed - Going to sleep position")
        skills.skill_executor.go_sleep()
    
    if controller_dict.button_just_pressed("X"):
        print("X pressed - Executing jump")
        skills.skill_executor.jump()
    
    # Handle continuous movements from joysticks
    # Forward/backward movement (left joystick Y axis)
    if abs(left_y) > JOYSTICK_THRESHOLD:
        if left_y > 0 and skills.skill_executor.current_skill != 'forward':
            print("Left stick forward - Starting forward movement")
            skills.skill_executor.start_continuous_movement('forward')
        elif left_y < 0 and skills.skill_executor.current_skill != 'backward':
            print("Left stick backward - Starting backward movement")
            skills.skill_executor.start_continuous_movement('backward')
    elif skills.skill_executor.current_skill in ['forward', 'backward']:
        skills.skill_executor.stop_continuous_movement()
    
    # Spin left/right movement (right joystick X axis)
    if abs(right_x) > JOYSTICK_THRESHOLD:
        if right_x > 0 and skills.skill_executor.current_skill != 'spin_right':
            print("Right stick right - Starting spin right movement")
            skills.skill_executor.start_continuous_movement('spin_right')
        elif right_x < 0 and skills.skill_executor.current_skill != 'spin_left':
            print("Right stick left - Starting spin left movement")
            skills.skill_executor.start_continuous_movement('spin_left')
    elif skills.skill_executor.current_skill in ['spin_left', 'spin_right']:
        skills.skill_executor.stop_continuous_movement()

def setup_serial_connection():
    """Establish serial connection to the Arduino"""
    global ser
    
    for port in SERIAL_PORTS:
        try:
            print(f"Attempting to connect to serial port: {port}")
            ser = serial.Serial(port, SERIAL_BAUD_RATE, timeout=SERIAL_TIMEOUT)
            # Wait for Arduino to reset after connection
            time.sleep(2)
            # Clear buffers at startup
            ser.reset_input_buffer()
            ser.reset_output_buffer()
            
            # Test the serial connection with a simple message
            #test_msg = "1500,1500,1500,1500,1500,1500,1500,1500,1500,1500,1500,1500\n"
            #ser.write(test_msg.encode('utf-8'))
            #ser.flush()
            #time.sleep(0.5)
            
            print(f"Serial connection established at {port}")
            return True
        except serial.SerialException as e:
            print(f"Error connecting to {port}: {e}")
            continue
    
    print("ERROR: Could not connect to any serial port. Please check Arduino connection.")
    return False

def main():
    """Main function to run the parallel control system"""
    global ser, imu
    
    print("Starting IK_moving_parallel.py - Controller-based robot control")
    
    # Ensure controller is initialized
    if not controller_dict.running:
        controller_dict.start_controller_reader()
    
    # Set up serial connection
    if not setup_serial_connection():
        return
    
    # Configure the skill executor with our move_legs function
    skills.skill_executor.set_move_legs_function(move_legs_to_pos)
    
    # Start IMU stabilizer
    imu = IMUStabilizer(update_hz=IMU_UPDATE_HZ)
    try:
        imu.start()
        # Ensure we zero reference once more after initial home pose is reached
        print("IMU stabilizer started")
    except Exception as e:
        print(f"IMU initialization failed: {e}")
        imu = None

    # Go to home position to start
    skills.skill_executor.go_home()
    # Give servos a moment to settle at home, then zero IMU reference so home is level
    if imu:
        time.sleep(0.3)
        imu.zero_reference()
        print("IMU zeroed at home pose")
    
    try:
        # Main control loop
        while True:
            # Process controller inputs
            process_controller_inputs()
            
            # Small delay to prevent high CPU usage
            time.sleep(0.01)
    
    except KeyboardInterrupt:
        print("\nShutting down...")
    except Exception as e:
        print(f"Error in main loop: {e}")
    finally:
        # Cleanup
        if skills.skill_executor.movement_in_progress:
            skills.skill_executor.stop_continuous_movement()
        
        if ser and ser.is_open:
            ser.close()
        
        controller_dict.stop_controller_reader()
        if imu:
            imu.stop()
        print("Shutdown complete")

if __name__ == "__main__":
    main() 

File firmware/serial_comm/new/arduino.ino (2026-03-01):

#include <Servo.h>

// Servo objects for each servo in the quadruped
Servo SFR, FFR, TFR;  // Front Right
Servo SFL, FFL, TFL;  // Front Lefta
Servo SBR, FBR, TBR;  // Back Right
Servo SBL, FBL, TBL;  // Back Left

// Servo pins for Arduino Mega
const int SFR_PIN = 7, FFR_PIN = 6, TFR_PIN = 5;  // Front Right Pins
const int SFL_PIN = 4, FFL_PIN = 3, TFL_PIN = 2;  // Front Left Pins
const int SBR_PIN = 8, FBR_PIN = 9, TBR_PIN = 10; // Back Right Pins
const int SBL_PIN = 11, FBL_PIN = 12, TBL_PIN = 13; // Back Left Pins

// Step data for each leg - Servo angles in microseconds 
// targets = [[0,5,15],[0,0,15],[0,-5,15]]
//const int FR_steps[18][3] = {{1278.0, 832.0, 1558.0}, {1278.0, 818.0, 1544.0}, {1278.0, 804.0, 1529.0}, {1278.0, 791.0, 1514.0}, {1278.0, 778.0, 1498.0}, {1278.0, 767.0, 1482.0}, {1278.0, 756.0, 1465.0}, {1278.0, 746.0, 1448.0}, {1278.0, 737.0, 1430.0}, {1278.0, 693.0, 1456.0}, {1278.0, 651.0, 1477.0}, {1279.0, 610.0, 1494.0}, {1279.0, 636.0, 1534.0}, {1279.0, 665.0, 1573.0}, {1279.0, 697.0, 1611.0}, {1279.0, 732.0, 1647.0}, {1278.0, 763.0, 1619.0}, {1278.0, 796.0, 1590.0}};
//const int FL_steps[18][3] = {{1260.0, 1837.0, 1054.0}, {1259.0, 1880.0, 1029.0}, {1259.0, 1921.0, 1008.0}, {1259.0, 1962.0, 990.0}, {1259.0, 1937.0, 950.0}, {1259.0, 1908.0, 911.0}, {1259.0, 1876.0, 873.0}, {1259.0, 1841.0, 837.0}, {1259.0, 1811.0, 864.0}, {1259.0, 1778.0, 894.0}, {1260.0, 1743.0, 926.0}, {1260.0, 1757.0, 940.0}, {1260.0, 1771.0, 955.0}, {1260.0, 1783.0, 971.0}, {1260.0, 1796.0, 986.0}, {1260.0, 1807.0, 1003.0}, {1260.0, 1818.0, 1020.0}, {1260.0, 1828.0, 1037.0}};
//const int BR_steps[18][3] = {{1254.0, 702.0, 1363.0}, {1254.0, 659.0, 1389.0}, {1254.0, 619.0, 1410.0}, {1254.0, 580.0, 1427.0}, {1254.0, 604.0, 1468.0}, {1254.0, 632.0, 1507.0}, {1254.0, 663.0, 1545.0}, {1254.0, 697.0, 1582.0}, {1254.0, 727.0, 1554.0}, {1254.0, 759.0, 1524.0}, {1254.0, 793.0, 1492.0}, {1254.0, 779.0, 1477.0}, {1254.0, 766.0, 1463.0}, {1254.0, 753.0, 1447.0}, {1254.0, 741.0, 1431.0}, {1254.0, 730.0, 1415.0}, {1254.0, 720.0, 1398.0}, {1254.0, 710.0, 1381.0}};
//const int BL_steps[18][3] = {{1282.0, 1760.0, 1033.0}, {1282.0, 1775.0, 1047.0}, {1282.0, 1789.0, 1063.0}, {1282.0, 1802.0, 1079.0}, {1282.0, 1814.0, 1095.0}, {1282.0, 1826.0, 1112.0}, {1282.0, 1836.0, 1130.0}, {1282.0, 1846.0, 1148.0}, {1282.0, 1855.0, 1166.0}, {1282.0, 1899.0, 1140.0}, {1283.0, 1941.0, 1118.0}, {1283.0, 1982.0, 1099.0}, {1283.0, 1957.0, 1057.0}, {1283.0, 1928.0, 1017.0}, {1283.0, 1896.0, 977.0}, {1283.0, 1860.0, 939.0}, {1283.0, 1829.0, 968.0}, {1282.0, 1796.0, 999.0}};

void setup() {
  Serial.begin(500000);
  Serial.setTimeout(50); 

  // Attach servos
  SFR.attach(SFR_PIN);
  FFR.attach(FFR_PIN);
  TFR.attach(TFR_PIN);

  SFL.attach(SFL_PIN);
  FFL.attach(FFL_PIN);
  TFL.attach(TFL_PIN);

  SBR.attach(SBR_PIN);
  FBR.attach(FBR_PIN);
  TBR.attach(TBR_PIN);

  SBL.attach(SBL_PIN);
  FBL.attach(FBL_PIN);
  TBL.attach(TBL_PIN);

  // Front Right (SFR, FFR, TFR)
  SFR.writeMicroseconds(1283);  // from your FR_steps first row
  FFR.writeMicroseconds(832);
  TFR.writeMicroseconds(1558);

  // Front Left (SFL, FFL, TFL)
  SFL.writeMicroseconds(1324);  // from your FL_steps first row
  FFL.writeMicroseconds(1743);
  TFL.writeMicroseconds(926);

  // Back Right (SBR, FBR, TBR)
  SBR.writeMicroseconds(1300);  // from your BR_steps first row
  FBR.writeMicroseconds(793);
  TBR.writeMicroseconds(1492);

  // Back Left (SBL, FBL, TBL)
  SBL.writeMicroseconds(1351);  // from your BL_steps first row
  FBL.writeMicroseconds(1760);
  TBL.writeMicroseconds(1033);
  // --- end ---

}

void loop() {
  // We expect 12 integers each time (SFR, FFR, TFR, SFL, FFL, TFL, SBR, FBR, TBR, SBL, FBL, TBL)
  while (Serial.available()) {
    // Read a line of text up to '\n'
    String line = Serial.readStringUntil('\n');
    // Example line: "1500,1450,1400,1600,1550,1500,1300,1250,1200,1400,1350,1300"

    // Parse the 12 integers
    int values[12];
    int index = 0;

    // Split the line by commas
    char * c_line = strdup(line.c_str());
    char * token = strtok(c_line, ",");
    while (token != NULL && index < 12) {
      values[index++] = atoi(token);
      token = strtok(NULL, ",");
    }
    free(c_line);

    // If we got exactly 12 values, update the servos
    if (index == 12) {
      // Assign them to each servo
      SFR.writeMicroseconds(values[0]);
      FFR.writeMicroseconds(values[1]);
      TFR.writeMicroseconds(values[2]);

      SFL.writeMicroseconds(values[3]);
      FFL.writeMicroseconds(values[4]);
      TFL.writeMicroseconds(values[5]);

      SBR.writeMicroseconds(values[6]);
      FBR.writeMicroseconds(values[7]);
      TBR.writeMicroseconds(values[8]);

      SBL.writeMicroseconds(values[9]);
      FBL.writeMicroseconds(values[10]);
      TBL.writeMicroseconds(values[11]);

      // Optional debug
      Serial.print("Updated servo positions: ");
      Serial.println(line);
    }
  }
}

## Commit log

2024-10-25 upload easy reading working code in Arduino
2024-10-25 add IMU gif
2024-10-25 leg design
2024-10-30 added final leg stls
    [buck_converter_scan.stl, final_legtest_with_joints.f3d]
2024-11-11 add calibration resources
2024-11-11 add calibration tools
    [arm_for_calibration_tool.stl, buck_converter_scan.stl, femur_calibration_tool.stl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]
2024-11-11 fusion files added
    [BL.f3d, BR v7.f3d, Base_v2.stl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]
2024-11-11 urdf file image
2024-11-11 add direction for urdf usage
2024-11-14 update stl's
    [left.3mf, left.stl, right.stl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]
2024-11-14 add FR leg
    [bearings_filler_x5.stl, femur_down_FL.stl, femur_up_FL.stl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]
2024-11-14 update body
    [ass.stl, face.stl, left.stl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]
2024-11-18 improve precision and add servo calibration+IK
2024-11-18 add br leg
    [femur_down_BR.3mf, femur_down_BR.stl, femur_up_BR.stl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]
2024-11-18 add BL and FR leg
    [femur_down_BL.stl, femur_down_BR.3mf, femur_down_FR.stl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]
2024-11-25 add new servo holder and testing support
    [BR.f3d, soulder_femur_connector_BL.stl, soulder_femur_connector_BR.stl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]
2024-12-20 add fun pic for URDF
2024-12-20 add new body URDF
    [body_urdf.f3d]
2024-12-30 new urdf
2025-01-21 Update serial_sender.py
    Completed communication for IK to Arduino
2025-01-21 Update sketch_oct27a.ino
    Completed Serial Receiving of Angles from RPI to Move each servo
2025-02-11 add new leg files
    [BL.f3d, BL_ankle_left.stl, BL_ankle_right.stl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]
2025-02-11 change supports
    [stick_base.stl, stick_bearings_fill.stl, stick_grip.stl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]
2025-02-18 new body design uploaded
    [ass.stl, battery_box_holder.stl, bottom_base(printed).stl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]
2025-02-20 revise and update
    [battery_box_holder(printed).stl, battery_box_holder.stl, lid_battery.stl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]
2025-02-20 minor changes
    [plaque_right(printed).stl, plaque_right.3mf, top(printed).stl]
2025-02-20 add gifs for assembly
2025-02-20 update printed stls
    [front_face(print).stl, internal_infrastructure(printed).stl]
2025-03-18 need IK adjustemnt of the functions
    [BL_femur_servo1.stl, BL_femur_servo2.stl, BL_femur_servo_v11.stl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]
2025-03-22 BR leg working
2025-03-22 files prointed
    [battery_box_holder(printed).stl, lid_battery(printed).stl, lid_battery.stl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]
2025-04-03 make ALMOST inverse kinematic works for all legs
2025-06-20 remove sim
    [BL_femur_servo1.stl, BL_femur_servo2.stl, BL_femur_servo_v11.stl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]
2025-08-06 docs: create documetation for Botzo
    This commit creates and moves some of the existing documentation to a
    centralized place in `/docs` to which material mkdocs is used to
    generate beautiful documentation that can be hosted using github pages
    by automating a github action to automatically publish it.
    Futhermore, the assets have been moved to `/docs/assets`, which is also
    part of #6 idea.
2025-09-15 clean and improve structure. Fixes #6
    [servo_DEG-PWM.xlsx]
2025-10-03 improve documentation
    [BL.f3d, BL_ankle_left.stl, BL_ankle_right.stl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]
2025-10-05 improve and fix pybullet scripts
    [BL_femur_servo_v11.stl, BL_foot1.stl, BL_leg_ankle_v11.stl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]
2026-02-26 add scripts for raspberry pi
2026-02-26 add urdf for ros2 jazzy
    [BL_femur_collision.stl, BL_femur_visual.stl, BL_shoulder_collision.stl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]
2026-02-28 setup rviz botzo
    [BL_femur_collision.stl, BL_femur_servo.stl, BL_femur_visual.stl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]
2026-03-01 new urdf with new materials
    [BL_femur.stl, BL_femur_servo.stl, BL_hip_holder.stl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]
2026-03-01 make sim work with new urdf
    [BL_femur.stl, BL_femur_servo.stl, BL_hip_holder.stl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]
